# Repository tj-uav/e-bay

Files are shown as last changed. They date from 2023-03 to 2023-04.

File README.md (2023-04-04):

# e-bay
Electronics bay PCB for avalon

See Avalon X -> Improvements -> Ebay for the full MCAD assembly.

Designed to take 3-4S battery input through an XT60 connector and power a Pixhawk 2.4.8, Raspberry Pi 4, 5.5V Servo rail, Bullet AC, camera gimbal, plus one extra XT60 connector. Requires three buck converter modules (The servo rail buck must be rated for 5A, the other two may be between 3A and 5A). The Raspberry Pi buck module should be set to 5V flat. The Pixhawk buck module should be set to around 5.3V. The servo rail buck module should be set to 5-5.5V. Use a wire to connect the two PCBs, with the left side PCB receiving power from the battery and the right side PCB receiving power from the left. Because of a CAD mistake, the wire needs to be soldered to the right side PCB, while the left side can support an XT60 connector. Use 16AWG or thicker wire to handle high ish currents.

Molex cables going to the Pixhawk should have the same pinout on both ends of the cable (i.e. pin 1 is power). This is opposite of pixhawk convention, which mirrors the connector pinout on either end. Do NOT use pixhawk cables on this PCB.

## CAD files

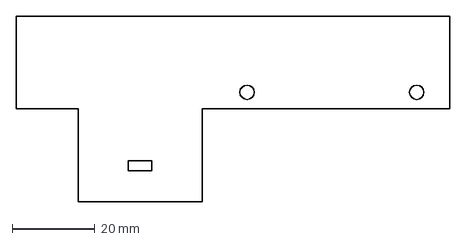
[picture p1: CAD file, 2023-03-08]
clamp keepout.dxf
105.0 x 45.0 mm

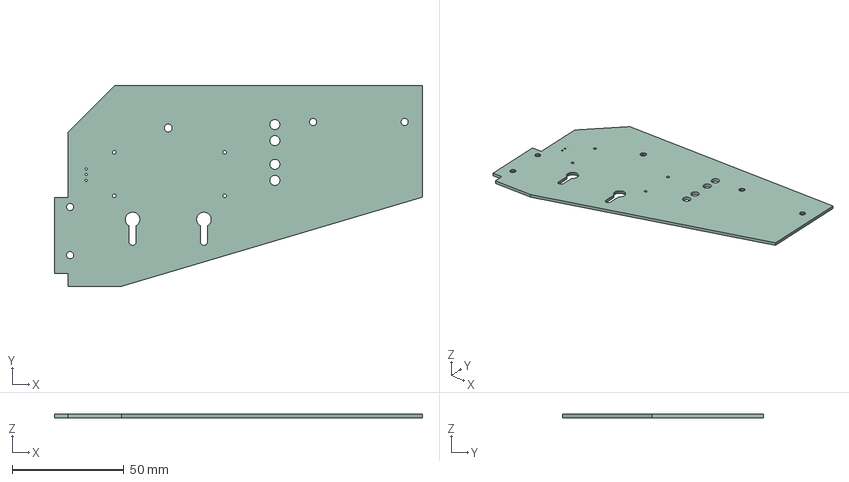
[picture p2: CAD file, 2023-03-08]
left-side/left-side.step
165.0 x 90.0 x 1.58 mm

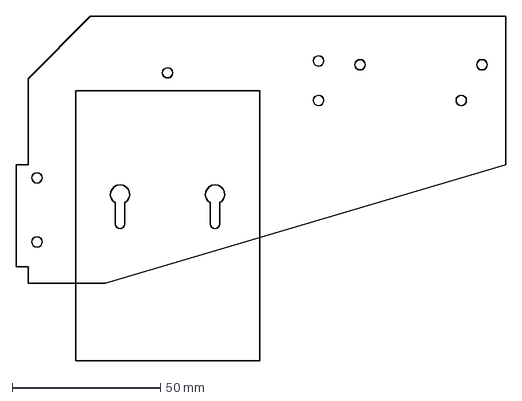
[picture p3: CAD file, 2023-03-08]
pcb outline.dxf
165.0 x 116.0 mm

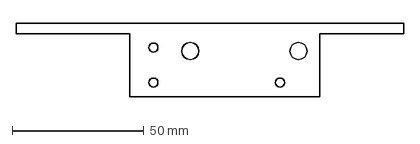
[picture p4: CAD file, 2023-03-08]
plate keepout.dxf
147.0 x 28.0 mm

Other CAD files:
right-side/right-side.step

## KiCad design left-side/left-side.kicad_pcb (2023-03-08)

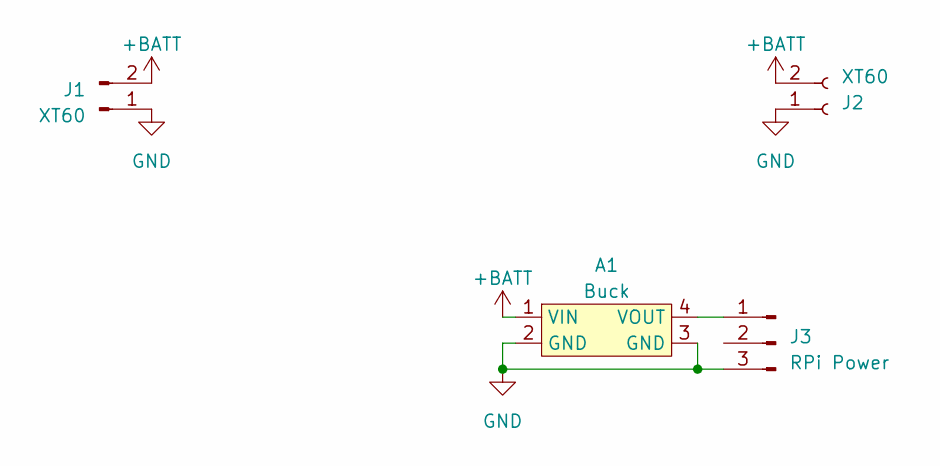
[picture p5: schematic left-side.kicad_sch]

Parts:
A1: Buck
J1: XT60; AMASS_XT60-M_1x02_P7.20mm_Vertical
J2: XT60; AMASS_XT60-F_1x02_P7.20mm_Vertical
J3: RPi Power; PinHeader_1x03_P2.54mm_Vertical

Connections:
+BATT: A1.1 (VIN), J1.2, J2.2
GND: A1.2 (GND), A1.3 (GND), J1.1, J2.1, J3.3
unnamed: A1.4 (VOUT), J3.1

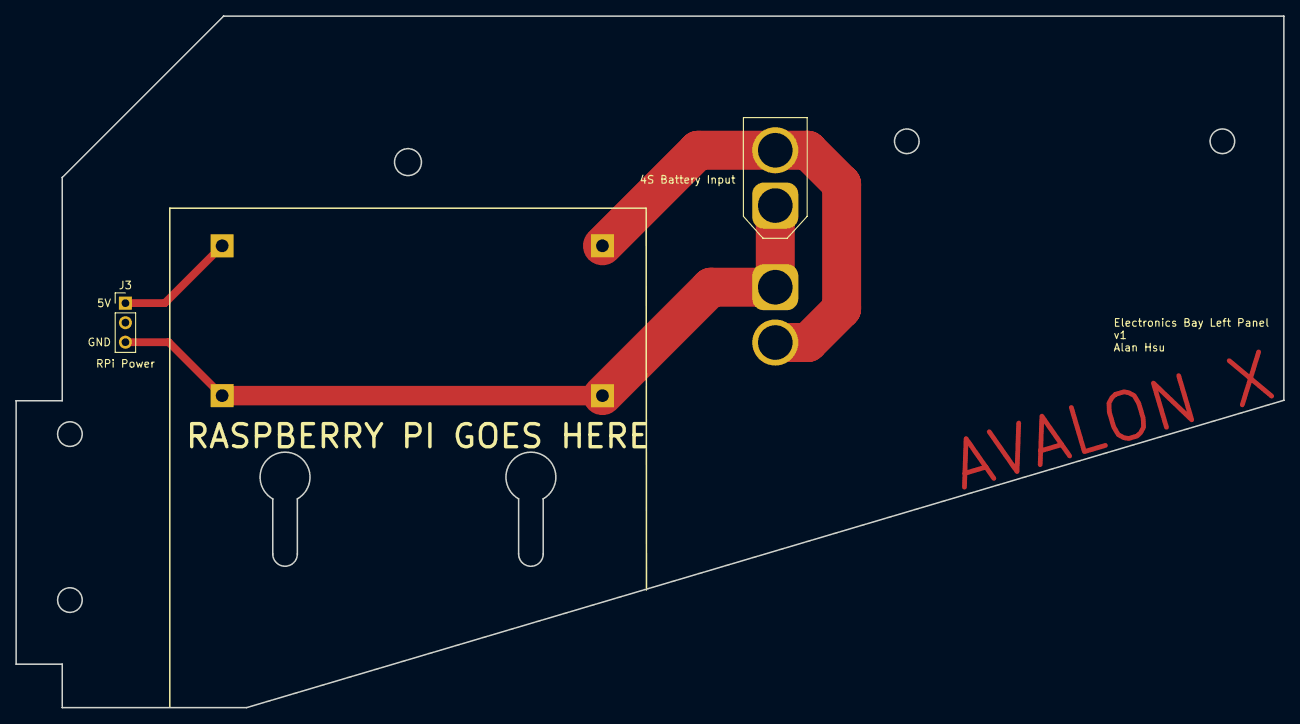
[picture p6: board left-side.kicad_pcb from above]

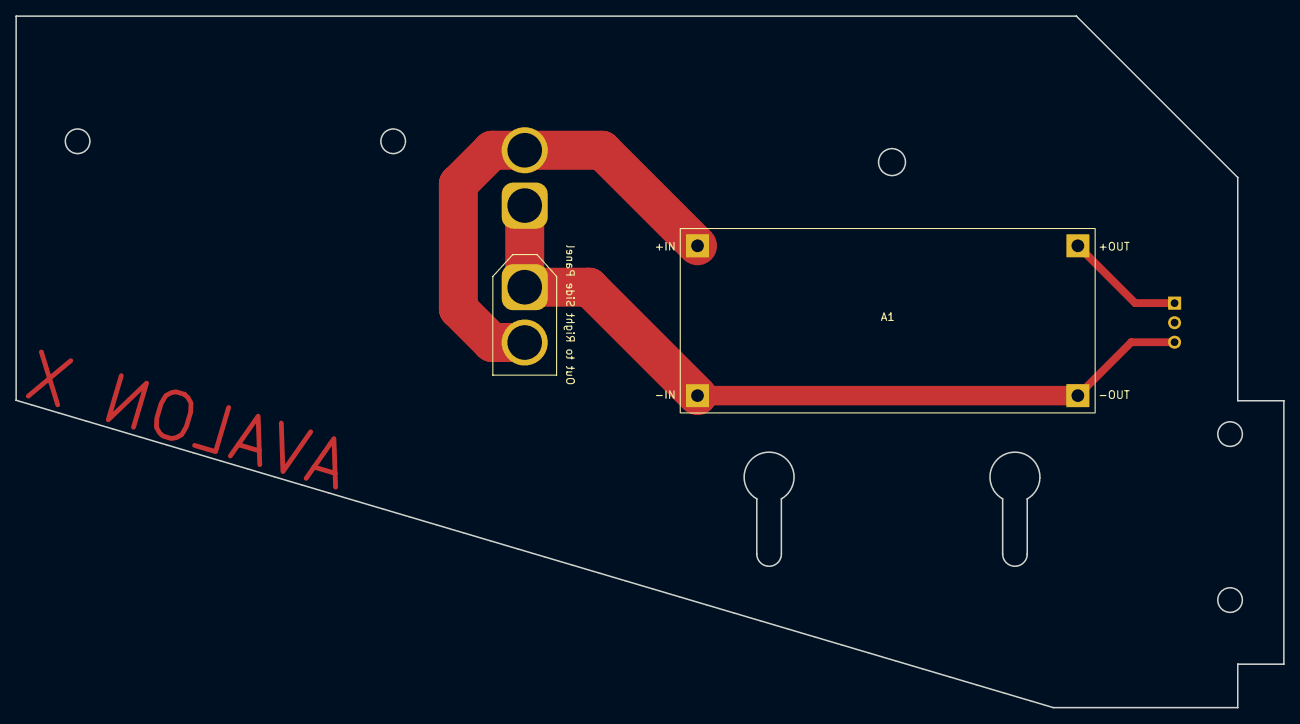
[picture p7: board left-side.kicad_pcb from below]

Board: 2 copper layers, 165.0 x 90.0 mm, 4 parts (2 on the bottom side), 3 nets.

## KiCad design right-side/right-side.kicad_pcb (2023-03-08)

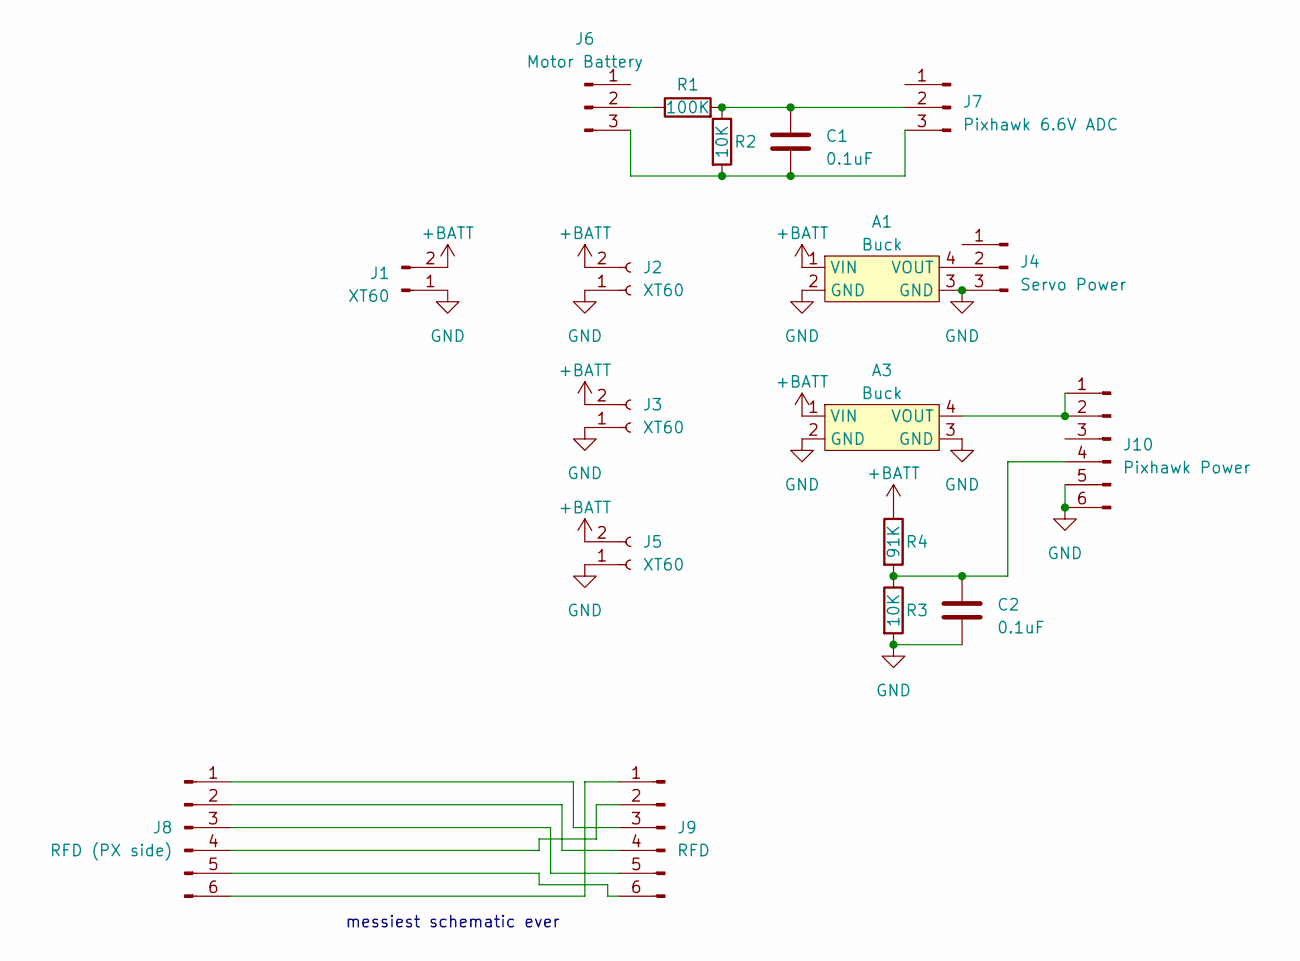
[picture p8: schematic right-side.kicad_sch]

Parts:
A1, A3: Buck
C1, C2: 0.1uF; C_Disc_D5.0mm_W2.5mm_P5.00mm
J1: XT60; AMASS_XT60-M_1x02_P7.20mm_Vertical
J2, J3, J5: XT60; AMASS_XT60-F_1x02_P7.20mm_Vertical
J4: Servo Power; PinHeader_1x03_P2.54mm_Vertical
J6: Motor Battery; PinHeader_1x03_P2.54mm_Vertical
J7: Pixhawk 6.6V ADC; Hirose_DF13-03P-1.25DSA_1x03_P1.25mm_Vertical
J8: RFD (PX side); Hirose_DF13-06P-1.25DSA_1x06_P1.25mm_Vertical
J9: RFD; PinHeader_1x06_P2.54mm_Vertical
J10: Pixhawk Power; Hirose_DF13-06P-1.25DSA_1x06_P1.25mm_Vertical
R1: 100K; R_Axial_DIN0207_L6.3mm_D2.5mm_P10.16mm_Horizontal
R2, R3: 10K; R_Axial_DIN0207_L6.3mm_D2.5mm_P10.16mm_Horizontal
R4: 91K; R_Axial_DIN0207_L6.3mm_D2.5mm_P10.16mm_Horizontal

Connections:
+BATT: A1.1 (VIN), A3.1 (VIN), J1.2, J2.2, J3.2, J5.2, R4.1
GND: A1.2 (GND), A1.3 (GND), A3.2 (GND), A3.3 (GND), C2.2, J1.1, J2.1, J3.1, J4.3, J5.1, J10.5, J10.6, R3.2
unnamed: A1.4 (VOUT), J4.2
unnamed: A3.4 (VOUT), J10.1, J10.2
unnamed: J6.2, R1.1
unnamed: C1.2, J6.3, J7.3, R2.2
unnamed: C1.1, J7.2, R1.2, R2.1
unnamed: J8.1, J9.3
unnamed: J8.2, J9.4
unnamed: J8.3, J9.5
unnamed: J8.4, J9.2
unnamed: J8.5, J9.6
unnamed: J8.6, J9.1
unnamed: C2.1, J10.4, R3.1, R4.2

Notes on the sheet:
messiest schematic ever

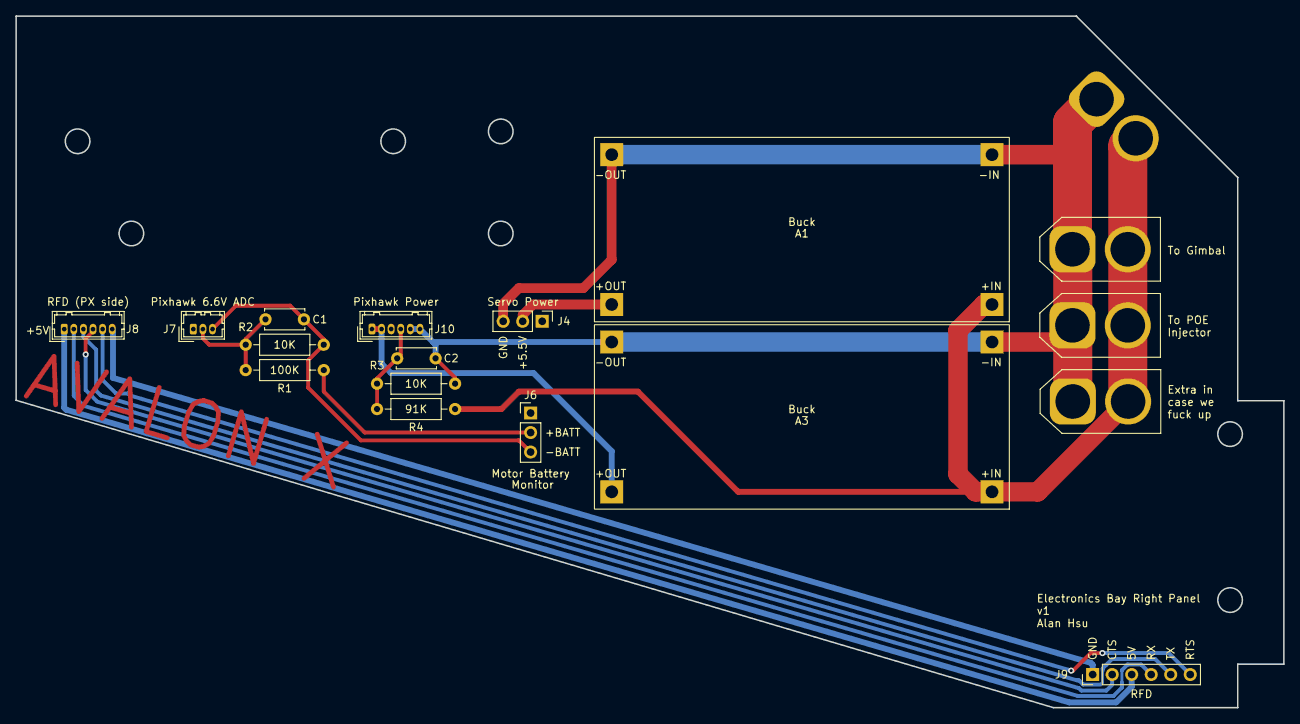
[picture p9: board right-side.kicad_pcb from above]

Board: 2 copper layers, 165.0 x 90.0 mm, 18 parts (1 on the bottom side), 14 nets.

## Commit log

2023-03-03 first work
    [left-side.kicad_pcb, left-side.kicad_sch, pcb outline.dxf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]
2023-03-03 update outlines, finish left side
    [left-side.kicad_pcb, pcb outline.dxf, right-side.kicad_pcb]
2023-03-08 finalize both panels
    [clamp keepout.dxf, left-side.kicad_pcb, pcb outline.dxf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]
2023-03-08 gerber export
    [left-side-B_Cu.gbr, left-side-B_Mask.gbr, left-side-B_Paste.gbr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]
2023-03-08 gerber zips and step exports
    [left-side.step, right-side.step]
